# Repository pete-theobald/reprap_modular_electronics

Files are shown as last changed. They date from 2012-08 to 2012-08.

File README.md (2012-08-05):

reprap_modular_electronics
==========================

Licence
-------
reprap modular electronics by Peter Theobald is licensed under a
Creative Commons Attribution-NonCommercial-ShareAlike 3.0 Unported
License.
Based on a work at
https://github.com/pete-theobald/reprap_modular_electronics.

Overview
--------
This project is intended to address a common issue with reprap
electronics, boards are monolithic, high cost and support a
predetermined set of components. Adding more motors, extruders, fans etc
than supported by your board needs a full upgrade.

This project intends to build a series of modules that can be
connected in parrallel with each unit able to control exactly one
stepper motor, 2x endstops, 1x heated device (extruder or bed) and one
fan. The modules will be as low cost as possible and be designed to
offload as much processing onto a host computer as possible. They will
still require a small controller module which will be tasked with
ensuring that stepper motors are controlled to a specific time base.

Details of modules
------------------

MCU
---
This project uses a low cost microchip pic MCU as its main processor.
The chip is available for around £1 and programmers are easily
available. This chip could easily be swapped for an arduino compatible 
chip. The chip is responsible for running PWM control loops (x2) and
listening for stepper commands on the bus and passing them to the
stepper driver.

Addressing
----------
The modules address can be set using 8 jumpers. The values are read by
the pic using the internal weak pullups meaning a closed jumper is read
as zero. The value on the port should be inverted so a closed jumper 
reads as a one. The jumpers are intended to be closed with solder to
keep costs low.
The MCU will use its UART to listen for messages. The RX pin is
connected to a bus. No bus drivers are included as the distance between
modules is intended to be small. The MCU will expect its address to be
sent in 9 bit format, i.e. 9th bit indicates an address byte.
The host controller software is responsible for mapping board addresses
to individual motors etc.

Stepper driver
--------------
The stepper module uses an Allegro A4982 stepper driver. All digital
pins on the chip are accessible to the MCU. The stepper driver will be
controlled by passing an absolute intended position for the stepper.
The stepper driver is intended to be fixed to a 1inch square heatsink.

Heater
------
The board contains a power mosfet (n channel) and a thermistor
PIDconnection. The MCU will run a pid control loop to regulate the
temperature. The PID constants and target will be setup remotely,
however there is currently no provision for monitoring the temperature
remotely.

End stops
---------
Connectors are included for end stops containing gnd, 5v and signal
lines. The end stop needs to be able to provide a digital output.

Fan
---
A fan header is included that can support 2, 3 and 4 pin pc fans.
The MCU can control the fan using a PWM signal. A jumper allows the pwm
signal to control either a mosfet on the 12v connector or directly to
the 4th pin for 4 pin fan connectors.
The possible states of the jumper are as follows
* No jumper - Continuous voltage supplied
* 2/3pin mode - Voltage controlled by PWM signal
* 4pin mode - PWM connected to pwm pin. Continuous voltage supplied

Components
----------
Below list shows prices for individual components in small quantitites

Part     Value          Device         Package           Library                 Sheet

ADDRESS  8WAYJUMPER     8WAYJUMPER     8WAYJUMPER        ics                     1		n/a
BUS                     PINHD-1X3/90   1X03/90           pinhead                 1		M22-2035005 50way right angle header £1.30 @10
C1                      C-EUC0603K     C0603K            rcl                     1		
C2                      C-EUC0603K     C0603K            rcl                     1
C3                      C-EUC0603K     C0603K            rcl                     1
C4                      C-EUC0603K     C0603K            rcl                     1
C5                      C-EUC0603K     C0603K            rcl                     1
C6                      CPOL-EUE2-5    E2-5              resistor                1
C7                      C-EUC0603K     C0603K            rcl                     1
EXTRUDE                 PINHD-1X4/90   1X04/90           pinhead                 1		M22-2035005 50way right angle header £1.30 @10
FAN                     PINHD-1X4/90   1X04/90           pinhead                 1		M22-2035005 50way right angle header £1.30 @10
IC1      AD820R         AD8541R        SO8               analog-devices          1		£0.60 @10
JP3                     PINHD-1X6/90   1X06/90           pinhead                 1
JP4                     JP2E           JP2               jumper                  1
MOTOR                   PINHD-1X4/90   1X04/90           pinhead                 1		M22-2035005 50way right angle header £1.30 @10
POWER                   PINHD-1X6/90   1X06/90           pinhead                 1		M22-2035005 50way right angle header £1.30 @10
Q3       FDN360P        FDN360P        SUPER-SOT3        transistor-power        1
Q4       BSS123         BSS123         SOT23             transistor-small-signal 1
R1                      R-EU_R0603     R0603             rcl                     1
R2                      R-EU_R0805     R0805             resistor                1
R3                      R-EU_R0805     R0805             resistor                1
R4                      R-EU_R0603     R0603             resistor                1
R5                      R-EU_R0603     R0603             rcl                     1
R6                      R-EU_R0603     R0603             rcl                     1
R7                      R-EU_R0603     R0603             rcl                     1
R8                      R-EU_R0603     R0603             rcl                     1
R9                      R-EU_R0603     R0603             rcl                     1
R10                     R-EU_R0603     R0603             rcl                     1
STOP+                   PINHD-1X3/90   1X03/90           pinhead                 1		M22-2035005 50way right angle header £1.30 @10
STOP-                   PINHD-1X3/90   1X03/90           pinhead                 1		M22-2035005 50way right angle header £1.30 @10
TX                      PINHD-1X1      1X01              pinhead                 1		M22-2035005 50way right angle header £1.30 @10
U$1      A4982          A4982          TSSOP24           ics                     1		£2.86 @10
U$2      PIC16F722-I/SS PIC16F722-I/SS SOP65P780X200-28N ics                     1		£0.96 @10
U$3      NMOSFET_DPACK  NMOSFET_DPACK  D-PAK_TO252AA     ics                     1		IPD170N04N G £0.29 @1

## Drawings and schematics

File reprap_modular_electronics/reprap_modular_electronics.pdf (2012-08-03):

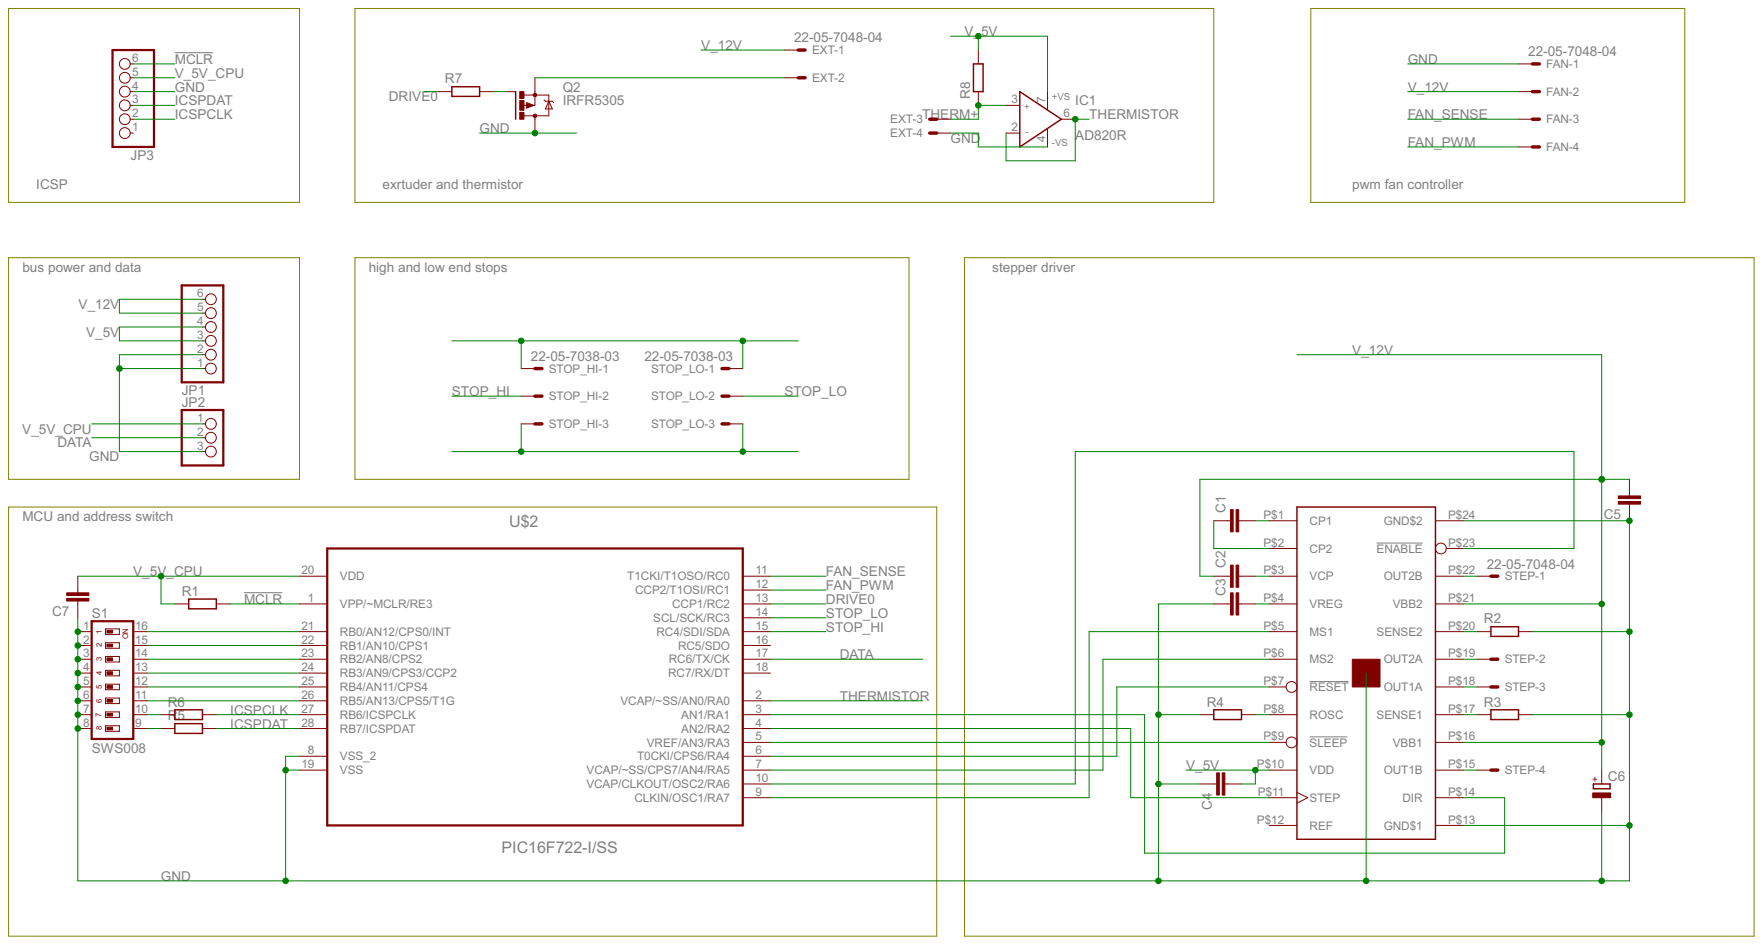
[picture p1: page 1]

FAN-1 FAN-2 FAN-3 FAN-4

STEP-1 STEP-2 STEP-3 STEP-4

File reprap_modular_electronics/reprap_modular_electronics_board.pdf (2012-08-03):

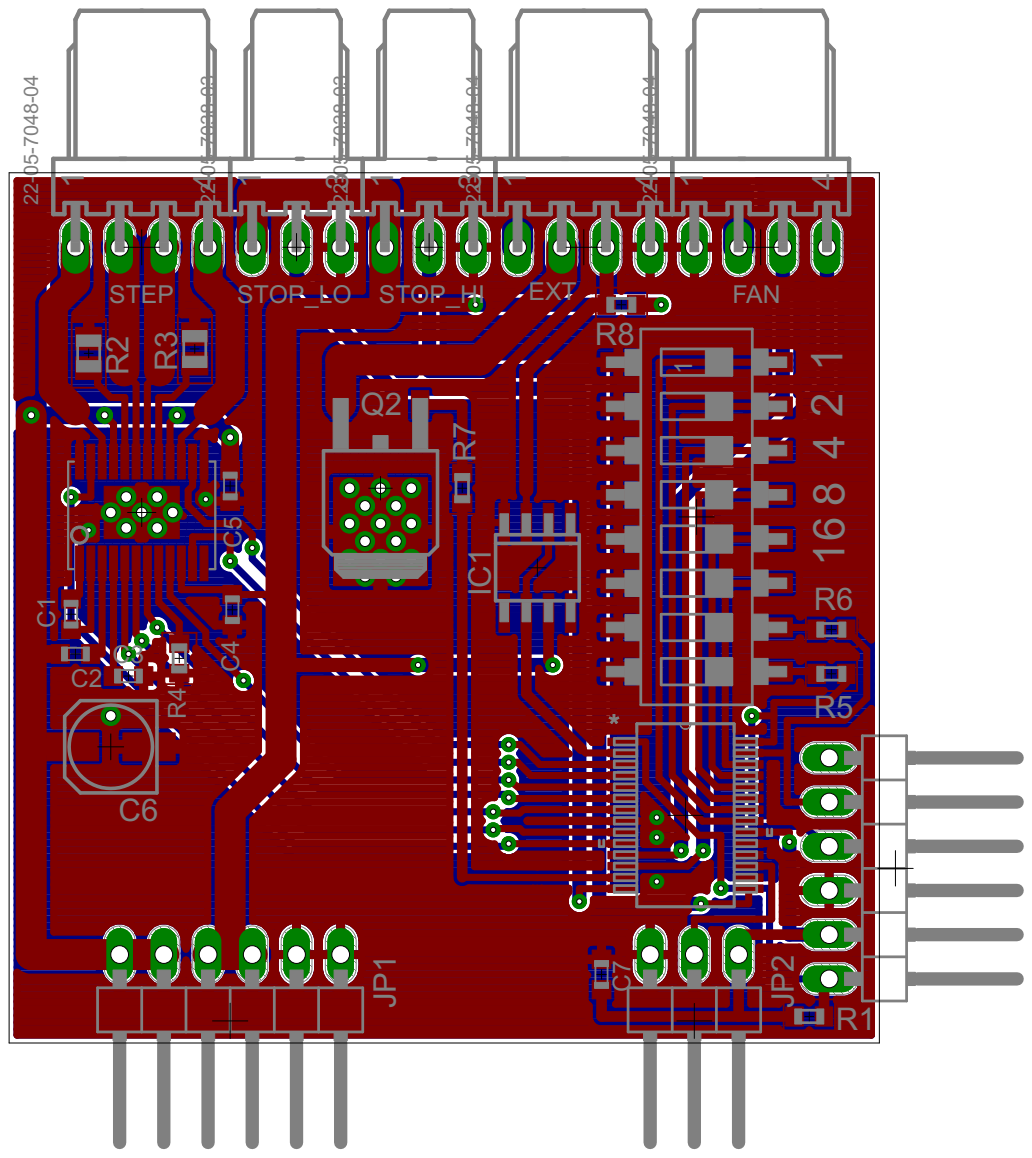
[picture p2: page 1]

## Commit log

2012-08-01 First attempt. Missing lots of components
    [reprap_modular_electronics.brd, reprap_modular_electronics.sch]
2012-08-03 Added dip switch Changed external connectors to edge fitted molex kk Added right angle pin headers for bus connection
    [reprap_modular_electronics.brd, reprap_modular_electronics.sch]
2012-08-05 Renamed original board as *_slave Created new board to handle PC interface and distribute power
    [reprap_modular_electronics.brd, reprap_modular_electronics.sch, reprap_modular_electronics_master.brd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]
2012-08-05 Completed prototype 1 for both boards. Sent for fabrication.
    [reprap_modular_electronics_master.brd, reprap_modular_electronics_master.sch, reprap_modular_electronics_slave.brd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]
